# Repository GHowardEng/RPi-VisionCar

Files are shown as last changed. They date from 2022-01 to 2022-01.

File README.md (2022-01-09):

# RPi-VisionCar
## OpenCV vision-based maze car project

piCar



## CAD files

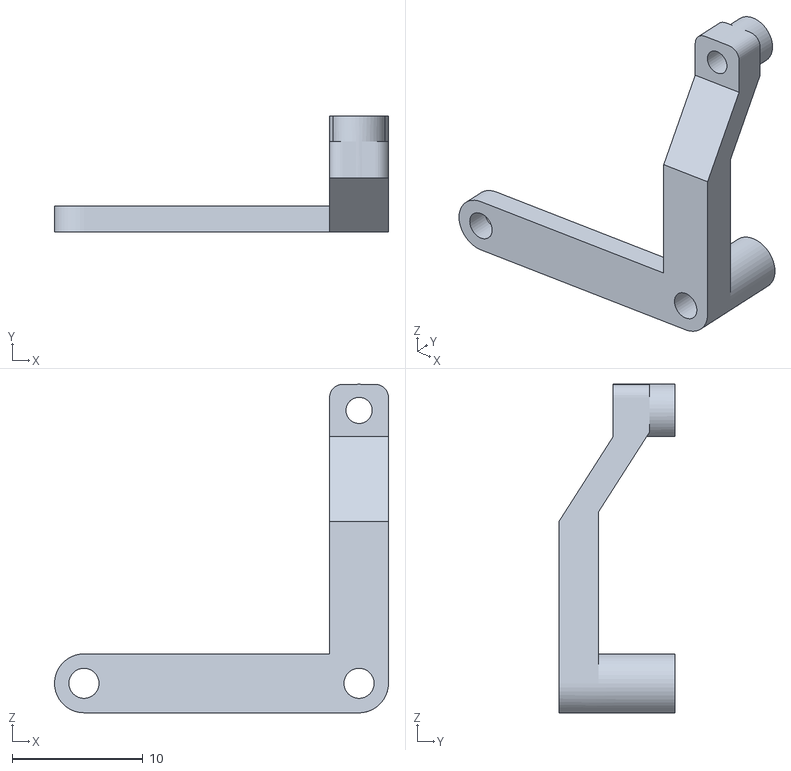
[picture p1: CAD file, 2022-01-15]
CAD/Components/CameraSpacer.stl
25.5 x 8.85 x 25.1

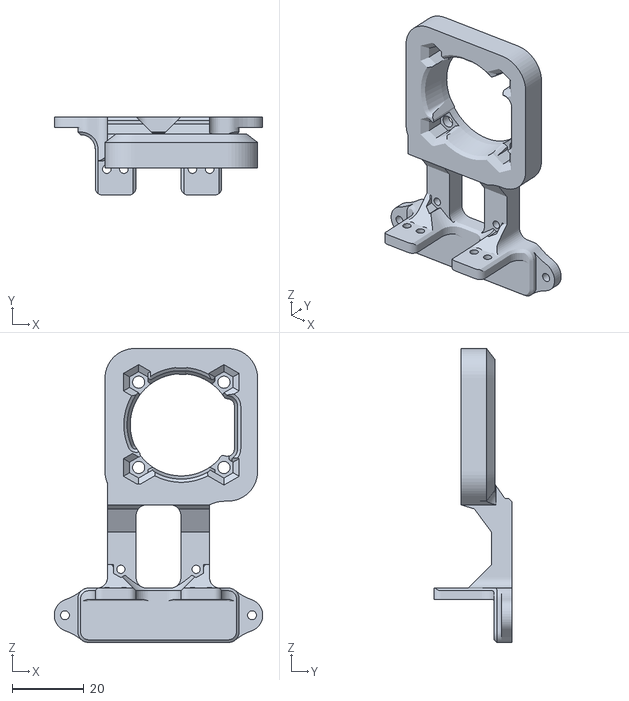
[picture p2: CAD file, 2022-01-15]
CAD/Components/SensorFanMount.stl
58.2 x 21.8 x 82.0

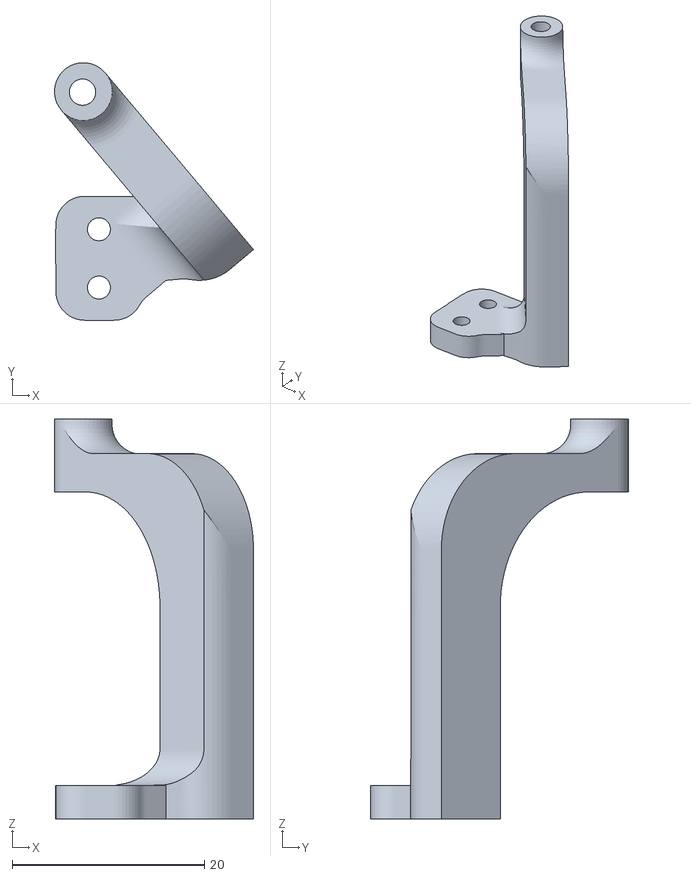
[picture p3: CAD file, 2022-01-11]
CAD/Components/PiMountFR.stl
20.7 x 26.8 x 41.6

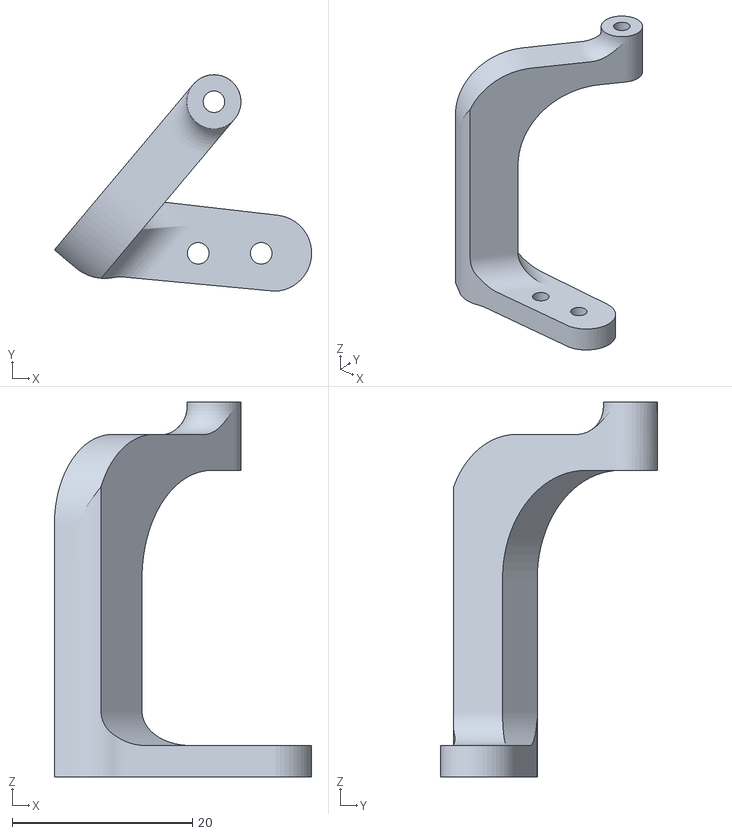
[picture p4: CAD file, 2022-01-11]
CAD/Components/PiMountLR.stl
28.6 x 24.1 x 41.6

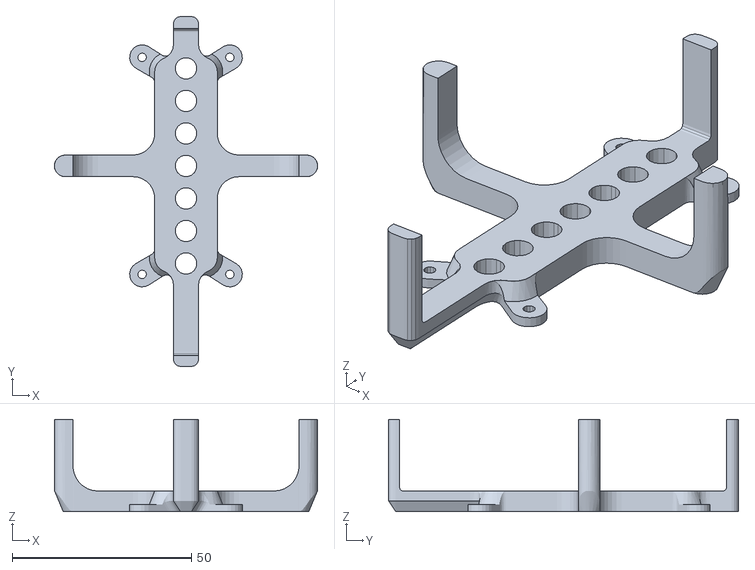
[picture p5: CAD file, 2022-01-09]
CAD/Components/BatteryBase.stl
73.5 x 97.8 x 25.7

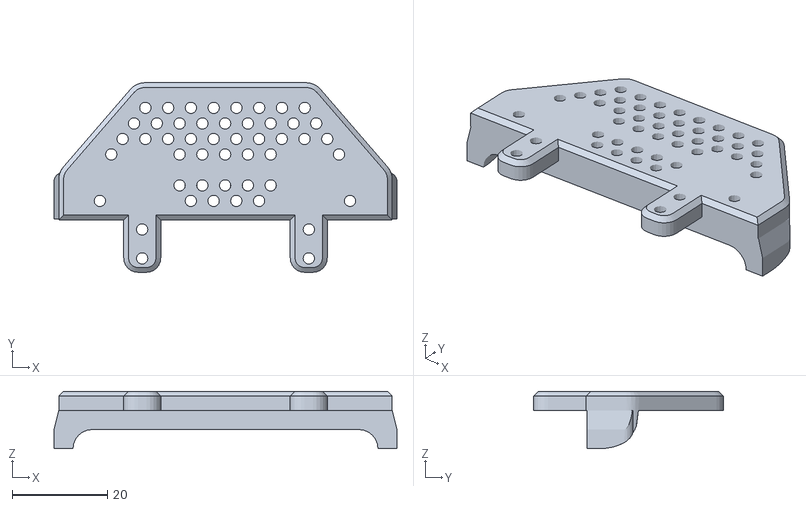
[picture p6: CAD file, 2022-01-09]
CAD/Components/CarFront.stl
72.0 x 39.8 x 12.0

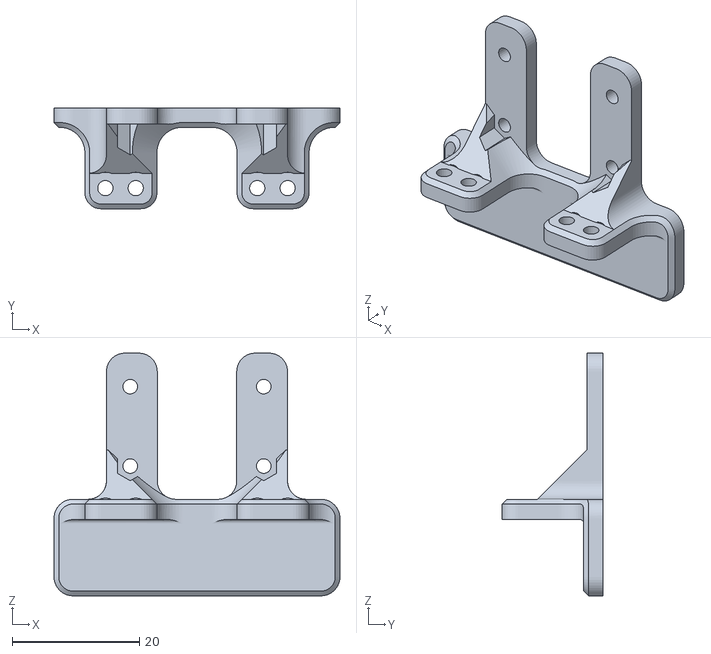
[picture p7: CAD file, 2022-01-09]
CAD/Components/Sensor Mount.stl
45.0 x 15.8 x 38.2

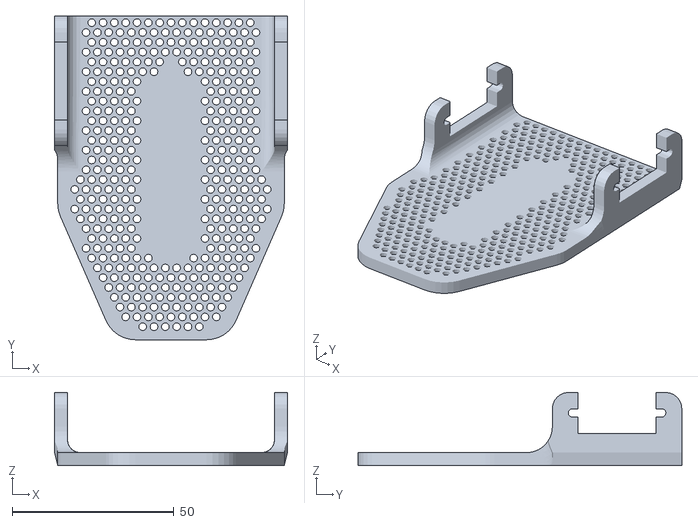
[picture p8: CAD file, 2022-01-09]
CAD/Components/CarBase v4.stl
72.0 x 100.0 x 22.6

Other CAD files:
CAD/Components/PiMountRR.stl

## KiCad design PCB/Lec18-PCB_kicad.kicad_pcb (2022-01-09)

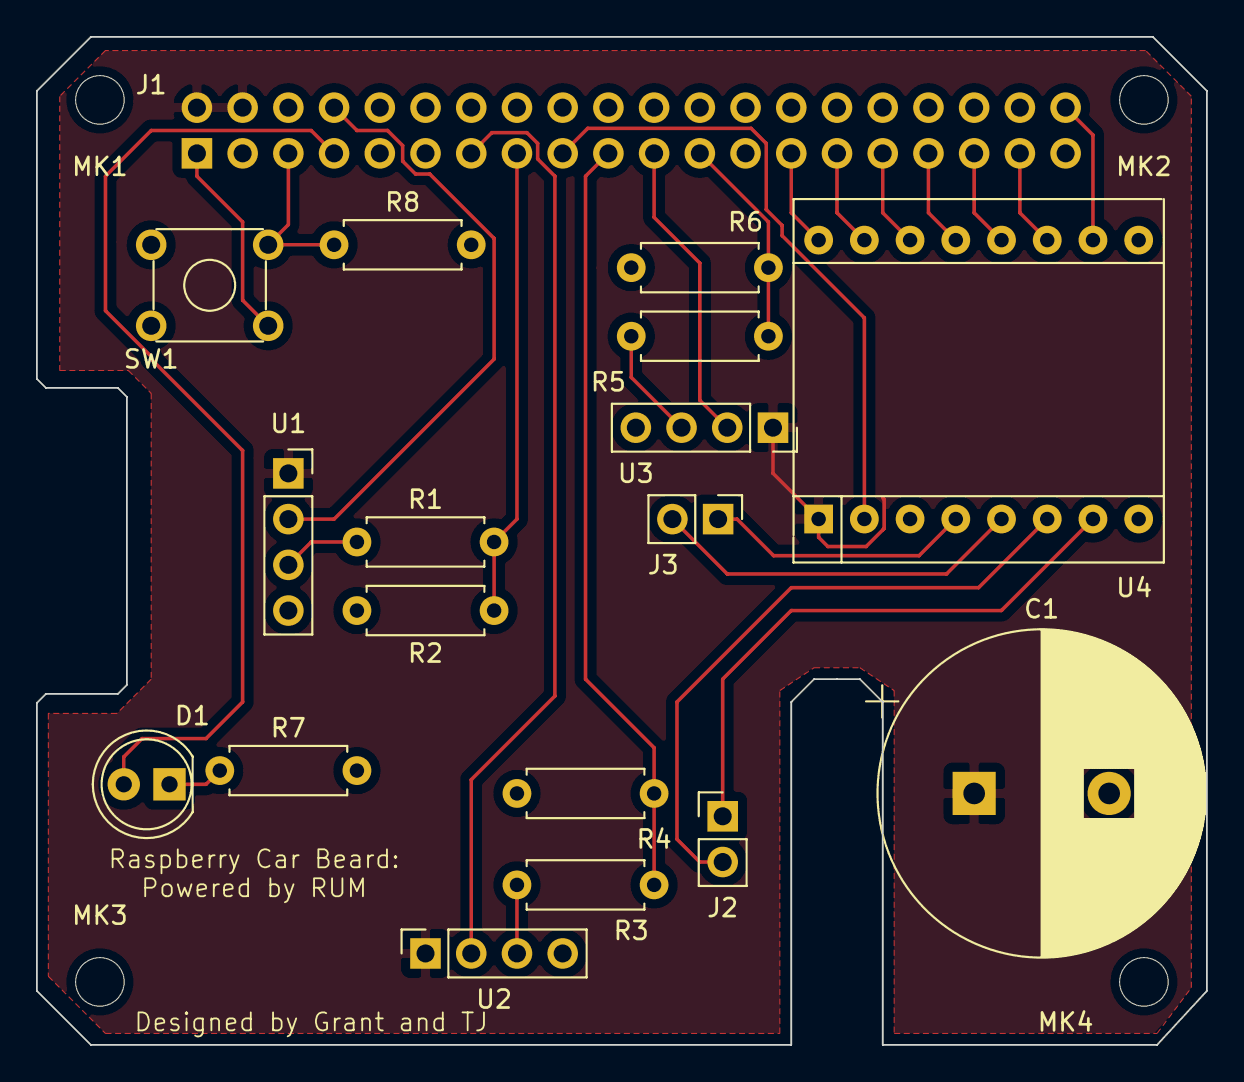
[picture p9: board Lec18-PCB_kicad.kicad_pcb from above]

Board: 2 copper layers, 65.0 x 56.0 mm, 22 parts (1 on the bottom side), 26 nets.

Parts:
C1: CAP; CP_Radial_D18.0mm_P7.50mm
D1: LED; LED_D5.0mm
J1: Raspberry_Pi_2_3; PinSocket_2x20_P2.54mm_Vertical
J2, J3: Conn_01x02_Male; PinHeader_1x02_P2.54mm_Vertical
MK1, MK2, MK3, MK4: M2.5; MountingHole_2.7mm_M2.5
R1, R2, R3, R4, R5, R6, R7, R8: R; R_Axial_DIN0207_L6.3mm_D2.5mm_P7.62mm_Horizontal
SW1: SW_Push_Dual; SW_TH_Tactile_Omron_B3F-10xx
U1, U2, U3: HC-SR04; PinSocket_1x04_P2.54mm_Vertical
U4: TB6612FNG_BREAKOUT; SparkFun_TB6612_foot

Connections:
+3V3: J1.1, J1.17, SW1.4, U4.2
+5V: C1.1, J1.2, J1.4, U1.1, U2.1, U3.1, U4.1
A01: J3.1, U4.4
A02: J3.2, U4.5
AIN1: J1.31, U4.14
AIN2: J1.29, U4.15
B01: J2.1, U4.7
B02: J2.2, U4.6
BIN1: J1.35, U4.12
BIN2: J1.37, U4.11
GND: C1.2, J1.6, J1.9, J1.14, J1.20, J1.25, J1.30, J1.34, J1.39, R2.2, R4.2, R6.2, R7.2, R8.2, U1.4, U2.4, U3.4, U4.3, U4.8, U4.9
LED: D1.2, J1.7
unnamed: D1.1, R7.1
P1_ECHO: J1.15, R1.2, R2.1
P2_ECHO: J1.19, R3.2, R4.1
P3_ECHO: J1.23, R5.2, R6.1
PUSH_BUTTON: J1.5, R8.1, SW1.2
PWMA: J1.27, U4.16
PWMB: J1.40, U4.10
STBY: J1.33, U4.13
U1_ECHO: R1.1, U1.3
U1_TRIG: J1.8, U1.2
U2_ECHO: R3.1, U2.3
U2_TRIG: J1.13, U2.2
U3_ECHO: R5.1, U3.3
U3_TRIG: J1.21, U3.2

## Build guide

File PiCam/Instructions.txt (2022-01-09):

To get the Raspberry Pi Cam V2.1 working with OpenCV

From: https://www.uco.es/investiga/grupos/ava/node/40

0) Make sure you have CMAKE installed

sudo apt-get update
sudo apt-get install cmake

1) Make sure camera is plugged into correct port
2) Turn on camera with sudo raspi-config
3) Copy raspicam-0.1.6 folder to Pi
4) Make raspicam project in a build folder

cd raspicam-0.1.6
mkdir build
cd build
cmake ..

5) Complete the install 

make
sudo make install
sudo ldconfig

6) Test by running the test build

Copy to your code folder the header file:
raspicam_cv.h

Add to your compile flags:
-I/usr/local/include/

Add to your link flags:
-lraspicam -lraspicam_cv 

* Note the >> operator was not implemented by the raspicam system, instead use:

cap.grab();
cap.retrieve(frame);

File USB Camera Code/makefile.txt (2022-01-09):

CC=g++

CFLAGS=-Wall `pkg-config --cflags opencv` -std=c++11 -c

LDFLAGS=-Wall `pkg-config --libs opencv` -o

all: cam

Sorting: main.o 
	$(CC) $(LDFLAGS) cam main.o -lwiringPi -lpigpio 
	
main.o: main.cpp
	$(CC) $(CFLAGS) main.cpp
	
clean:
	rm *o TestControl

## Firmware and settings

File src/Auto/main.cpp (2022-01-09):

#include <opencv2/opencv.hpp>
#include <opencv2/highgui/highgui.hpp>
#include "CControlPi.hpp"
#include "pigpio.h"
#include "wiringPi.h"
#include "CVision.hpp"
#include "libSonar.h"
#include <thread>
#include <iostream>
#include "raspicam_cv.h"


#define trigger1 15
#define echo1 3

#define trigger_left	2
#define echo_left		12

#define trigger_right	13
#define echo_right		14

using namespace std;
using namespace cv;


void imagefunc();

CControlPi ctrl;

void sonarPing();
void input_ch();


float distFront = 0;
float distRight = 0;
float distLeft = 0;

int result = 0;
int run = 0;
int turn = 0;
int right_count = 0;
string ch;

bool thread_pause;
bool thread_exit;

enum mode_state { MANUAL = 0, AUTO };

cv::Mat image;
cv::Mat crop;

int main()
{
	CVision vision;
	Mat frame;
	string tx;
	int input = 0;

	thread_exit = false;
	
	std::thread t1(&input_ch);
	t1.detach();
	
	std::thread t2(&imagefunc);
	t2.detach();	// Start image thread and detach
	
	waitKey(10);
	delay(2000);
	
	std::thread t3(&sonarPing);
	t3.detach();	// Start sonar measurement thread and detach
		
    while (ch != "q")
	{
		//vision.frame = crop;		// Input new camera image
		vision.frame = crop.clone();
		ctrl.get_data(DIGITAL, SW, input);
		
		thread_pause = true; 	// Pause image transmission thread
	
		result = vision.nav_vid(); // Process image and detect colour
		//cout << "Front: " << distFront << " cm. Left: " << distLeft << " cm. Right: " << distRight << "\n";

		imshow("result", vision.frame);
		waitKey(1);
	
		
		if (ch == "r")
		{
			run = 1;
			ctrl.set_data(DIGITAL, LED, 1);
		}
		
		if (ch == "x" || (run == 1 && input))
		{
			ch = "0";
			run = 0;
			right_count = 0;
			ctrl.stop();
			ctrl.drive = STOP;
			ctrl.set_data(DIGITAL, LED, 0);
		}
		


		
		//cout << "NAV\n";
		if (distFront > 15 && ctrl.drive == FORWARD)
		{
			if (result != 0)
			{
				if((vision.bound.x - (vision.frame.size().width - (vision.bound.x + vision.bound.width))) > 25)
				{
					cout << "\nRIGHT";
					ctrl.correct(RIGHT);
				}
					
				else if (((vision.frame.size().width - (vision.bound.x + vision.bound.width)) - vision.bound.x) > 25)
				{
					cout << "\nLEFT";
					ctrl.correct(LEFT);
				}
			}
		}
		

		if (result == GREEN)	// Turn based on navigation colour in picture
		{
			//cout << "\nGreen\n";
			//imshow("result", vision.frame);
			//waitKey(2);
			
			if(run && distFront < 13 && ctrl.drive == STOP)
			{
				turn = 1;
				ctrl.turn(RIGHT);
				right_count += 1;
				cout << right_count << "\n";
				while(distFront < 15){}
				turn = 0;
			}
			
			//cout << "\n" << vision.bound.x << "\n";
			//cout << vision.frame.size().width - (vision.bound.x + vision.bound.width) << "\n";
			
		}
		
		else if (result == RED)
		{
			
			//cout << "\nRed\n";
			//imshow("result", vision.frame);
			//waitKey(1);
			
			if(run && distFront < 13 && ctrl.drive == STOP)
			{
				turn = 1;
				ctrl.turn(LEFT);
				//cout << "\nRed\n";
				while(distFront < 15){}
				turn = 0;
			}
			
		}
					
		
	}

	ctrl.stop();
	cout << "Exit\n";
	
	delay(100);
	thread_exit = true;
	delay(500);
	ctrl.set_data(DIGITAL, LED, 0);
	return 0;
}



void imagefunc()
{
	raspicam::RaspiCam_Cv Camera;
    Camera.open();
	delay(1000);		// Open camera and give time for setup
	
	Camera.grab();
	Camera.retrieve ( image );	// Take new image from camera
	
	// Create rectangle object for cropping
	Rect box;
	box.x = 0;
	box.y = 400;	// Set box starting points
	box.width = image.size().width;
	box.height = image.size().height - box.y;	// Set box dimensions
	
	do
	{	
		Camera.grab();
		Camera.retrieve ( image );	// Take new image from camera
		flip(image, image, 0);		// Mirror vertically
		flip(image, image, 1);
		resize(image(box), crop, Size(), 0.45, 0.45);

		//imshow("Camera", image);
		//waitKey(10);
	} while (thread_exit != true);
	
	Camera.release();
	return;
}

void sonarPing()
{
	Sonar sonar1, sonar_left, sonar_right;
	
	sonar1.init(trigger1, echo1);
	sonar_left.init(trigger_left, echo_left);
	sonar_right.init(trigger_right, echo_right);
	
    float sample[4], sample_R[2], sample_L[2];
    
    do 
    {
		
		//delay(5);
		sample[3] = sample[2];
		sample[2] = sample[1];
		sample[1] = sample[0];
		sample[0] = sonar1.distance(20000);		// Shift samples
		
		if (sample[0] < sample[1] && sample[0] > sample[2])
		{
			distFront = sample[0];
		}
		else if(sample[0] > sample[1] && sample[0] < sample[2])
		{
			distFront = sample[0];
		}
		else if(sample[1] > sample[0] && sample[1] < sample[2])
		{
			distFront = sample[1];
		}
		else if(sample[1] > sample[2] && sample[1] < sample[0])
		{
			distFront = sample[1];
		}
		else if(sample[2] > sample[0] && sample[2] < sample[1])
		{
			distFront = sample[2];
		}
		else if(sample[2] > sample[1] && sample[2] < sample[0])
		{
			distFront = sample[2];
		}
		//cout << distFront << "\n";
			
		
		/*sample_R[1] = sample_R[0];
		sample_R[0] = sonar_right.distance(20000);		// Shift samples

		sample_L[1] = sample_L[0];
		sample_L[0] = sonar_left.distance(20000);		// Shift samples*/
		
		
		//distFront = (sample[0] + sample[1] + sample[2] + sample[3]) / 4; // Apply moving to average samples
		//distLeft = (sample_L[0] + sample_L[1]) / 2; // Apply moving to average samples
		//distRight = (sample_R[0] + sample_R[1]) / 2; // Apply moving to average samples 
		
		//distFront = sonar1.distance(25000);
		//distRight = sonar_right.distance(25000);
		//distLeft = sonar_left.distance(25000);
	
		if(distFront > 600)		// Sensor reads large distance when actually at zero
			distFront = 0;
		if(distRight > 600)		// Sensor reads large distance when actually at zero
			distRight = 0;
		if(distLeft > 600)		// Sensor reads large distance when actually at zero
			distLeft = 0;	
		
	if (distFront > 16 && run && !(turn))
	{
		//cout << "FWD\n";
		//ctrl.stop();
		ctrl.forward();
		ctrl.drive = FORWARD;	
	}
	else if(distFront < 11.5 && ctrl.drive == FORWARD && !(turn) && right_count < 6)
	{
		ctrl.stop();
		ctrl.drive = STOP;
		//delay(10);
	}
	if(ctrl.drive == FORWARD && distFront < 25 && right_count < 6)
	{
		ctrl.setSpeed(65);
	}
	else if (ctrl.drive == FORWARD && (distFront > 30 || right_count >= 6))
	{
		ctrl.setSpeed(85);
	}
	
	if (right_count >= 6 && distFront < 5)
	{
		ctrl.stop();
		ctrl.drive = STOP;
	}
		

	
					
	if ((ctrl.drive == FORWARD) && distLeft <= 2.5)
	{

	//ctrl.correct(RIGHT);
	//cout << "RIGHT, distLeft: " << distLeft << "\n";
	//delay(150);

	}
	else if ((ctrl.drive == FORWARD) && distRight <= 2.5)
	{
	
		//ctrl.correct(LEFT);
		//cout << "LEFT, distRight: " << distRight << "\n";
		//delay(150);
	
	}
	
		
	
	} while(thread_exit != true);
	
	return;
}

void input_ch()
{
	cout << "Auto mode running.";
	ch = "0";
	do
	{
		cin >> ch;
	}while(thread_exit != true);
	return;	
}

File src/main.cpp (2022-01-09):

#include <opencv2/opencv.hpp>
#include "CControlPi.hpp"
#include "pigpio.h"
#include "wiringPi.h"
#include "server.h"
#include "CVision.hpp"
#include "libSonar.h"
#include <thread>
#include <iostream>
#include "raspicam_cv.h"

#define trigger1 15
#define echo1 3

#define trigger_left	2
#define echo_left		12

#define trigger_right	13
#define echo_right		14

using namespace std;
using namespace cv;

Server serv;
void serverfunc();
void serverimagefunc();

CControlPi ctrl;

void sonarPing();
void status();

float distFront;
float distRight;
float distLeft;

int result = 0;

int run = 0;

bool thread_pause;
mutex mtx;

enum mode_state { MANUAL = 0, AUTO };
int mode = MANUAL;

cv::Mat image;
cv::Mat crop;

int main()
{
	CVision vision;
	Mat frame;
	string tx;
	int input = 0;
	
	
	serv._exit = false;
	std::thread t1(&serverfunc);
	t1.detach();	// Start server thread and detach
	
	// Wait until server starts up
	delay(3000);

	std::thread t2(&serverimagefunc);
	t2.detach();	// Start image thread and detach
	
	delay(2000);
	
	std::thread t3(&sonarPing);
	t3.detach();	// Start sonar measurement thread and detach
	
	std::thread t4(&status);
	t4.detach();
	
	cout << "\nServer Running. Send 'q' from Client to exit.\n";
	
    while (serv.str[0] != 'q')
	{
		crop.copyTo(vision.frame); 		// Input new camera image
		//vision.frame = image;
		ctrl.get_data(DIGITAL, SW, input);
		
	
		if (serv.str[0] == 'm')		// Switch modes when 'm' received
		{
			if (mode == MANUAL)
			{
				mode = AUTO;
				
				serv.reply = "AUTO MODE";
				cout << "\n" << serv.reply << "\n";
				send(serv.clientsock, serv.reply.c_str(), serv.reply.length(), 0);
			}
			else
			{
				mode = MANUAL;
				
				serv.reply = "MANUAL MODE";
				cout << "\n" << serv.reply << "\n";
				send(serv.clientsock, serv.reply.c_str(), serv.reply.length(), 0);
				ctrl.drive = STOP;
			}
			delay(1000);
		}
		
		if (mode == MANUAL)				// If in manual mode
		{
						
			thread_pause = false;		// Run image transmission thread
			delay(1);
			
			if(distFront < 10.5 && ctrl.drive == FORWARD)
			{
				ctrl.stop();
				ctrl.drive = STOP;
			}
			
			if (input)
				ctrl.stop();
			else
				ctrl.readInput(serv.str);	// Read manual inputs and control car
		}
		
		else 						// Else run in automatic mode
		{
			thread_pause = true; 	// Pause image transmission thread
		
			
			delay(100);
			cout << "Front: " << distFront << " cm. Left: " << distLeft << " cm. Right: " << distRight << "\n";
			
			
			if (serv.str[0] == 'r' || (run == 0 && input))
			{
				run = 1;
				ctrl.set_data(DIGITAL, LED, 1);
				
			}
			
			if (serv.str[0] == 'x' || (run == 1 && input))
			{
				run = 0;
				ctrl.stop();
				ctrl.drive = STOP;
				ctrl.set_data(DIGITAL, LED, 0);
				
			}
			
			if (run == 1)
			{
				if (distFront < 20)
					result = vision.nav_vid(); // Process image and detect colour
					serv.set_txim(vision.im);	// Transmit processed image	
					//imshow("vision", vision.im);
					//waitKey(1);
				if (ctrl.drive == STOP)
				{

					

				}
				
					
			}
		}

	}

	ctrl.stop();
	
	//serv._exit = true;
	delay(500);
	return 0;
}


// Start TCP server
void serverfunc()
{
	serv.start(4618);
}

// Send image to TCP server
void serverimagefunc()
{
	raspicam::RaspiCam_Cv Camera;
    Camera.open();
	delay(1000);		// Open camera and give time for setup
	
	Camera.grab();
	Camera.retrieve ( image );	// Take new image from camera
	
	// Create rectangle object for cropping
	Rect box;
	box.x = 100;
	box.y = 200;	// Set box starting points
	box.width = image.size().width - 2*box.x;
	box.height = image.size().height - 1.15*box.y;	// Set box dimensions
	
	do
	{	
		Camera.grab();
		Camera.retrieve ( image );	// Take new image from camera
		crop = image(box);
		flip(crop, crop, 0);		// Mirror vertically
		flip(crop, crop, 1);
		
		
		if(thread_pause == false)	// If not paused, set image for transmission
		{
			serv.set_txim(crop);
		}
		
	} while (serv._exit != true);
}

void sonarPing()
{
	Sonar sonar1, sonar_left, sonar_right;
	
	sonar1.init(trigger1, echo1);
	sonar_left.init(trigger_left, echo_left);
	sonar_right.init(trigger_right, echo_right);
	
    float sample[2], sample_R[2], sample_L[2];
    
    do 
    {
		//delay(5);
		
		/*sample[1] = sample[0];
		sample[0] = sonar1.distance(25000);		// Shift samples
		
		sample_R[1] = sample_R[0];
		sample_R[0] = sonar_right.distance(25000);		// Shift samples

		sample_L[1] = sample_L[0];
		sample_L[0] = sonar_left.distance(25000);		// Shift samples*/
		
		mtx.lock();
		/*distFront = (sample[0] + sample[1]) / 2; // Apply moving to average samples
		distLeft = (sample_L[0] + sample_L[1]) / 2; // Apply moving to average samples
		distRight = (sample_R[0] + sample_R[1]) / 2; // Apply moving to average samples
		*/
		distFront = sonar1.distance(25000);
		distRight = sonar_right.distance(25000);
		distLeft = sonar_left.distance(25000);
	
		if(distFront > 600)		// Sensor reads large distance when actually at zero
			distFront = 0;
		if(distRight > 600)		// Sensor reads large distance when actually at zero
			distRight = 0;
		if(distLeft > 600)		// Sensor reads large distance when actually at zero
			distLeft = 0;	
		mtx.unlock();
		
		if ((ctrl.drive == FORWARD) && distLeft <= 2.2)
		{
			mtx.lock();
			ctrl.correct(RIGHT);
			cout << "RIGHT, distLeft: " << distLeft << "\n";
			delay(100);
			mtx.unlock();
		}
		else if ((ctrl.drive == FORWARD) && distRight <= 2.2)
		{
			mtx.lock();
			ctrl.correct(LEFT);
			cout << "LEFT, distRight: " << distRight << "\n";
			delay(100);
			mtx.unlock();
		}
		
		if(distFront < 11.5 && ctrl.drive == FORWARD)
		{
			mtx.lock();
			ctrl.stop();
			ctrl.drive = STOP;
			mtx.unlock();
	

			if (result == GREEN)	// Turn based on navigation colour in picture
			{
				ctrl.drive = STOP;
				cout << "\nGreen\n";
				ctrl.turn(RIGHT);
			}
			
			else if (result == RED)
			{
				ctrl.drive = STOP;
				cout << "\nRed\n";
				ctrl.turn(LEFT);
			}
		}
			
		else if (distFront > 25.0 && mode == AUTO && run )
		{
			mtx.lock();
			ctrl.forward();
			ctrl.drive = FORWARD;
			mtx.unlock();
			
		}
	
	} while(serv._exit != true);
}

void status()
{
	do
	{
		while(mode != MANUAL){}
		delay(10);
		gpioWrite(LED, gpioRead (STBY) );
	} while(serv._exit != true);
}

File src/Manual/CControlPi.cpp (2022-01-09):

#include "CControlPi.hpp"
#include "pigpio.h"
#include "wiringPi.h"
#include "softPwm.h"

#include <iostream>

#define max 65
using namespace std;

CControlPi::CControlPi()
{
	wiringPiSetup();
	softPwmCreate (PWMa, 100, 100);
	softPwmCreate (PWMb, 100, 100);
	
	gpioInitialise();
	gpioSetMode(Ai1, PI_OUTPUT);
	gpioSetMode(LED, PI_OUTPUT);
	gpioSetMode(SW,	 PI_INPUT);
	gpioSetMode(Ai2, PI_OUTPUT);
	gpioSetMode(Bi1, PI_OUTPUT);
	gpioSetMode(Bi2, PI_OUTPUT);
	gpioSetMode(STBY, PI_OUTPUT);
	
	//CControlPi::stop();
}
bool CControlPi::get_data(int type, int channel, int &value)
{
	if (type == DIGITAL)
	{
		value = gpioRead (channel);
		return true;
	}
	
	else if (type == ANALOG)
	{
		unsigned char inBuf[3];
		char cmd[] = { 1, 128, 0 };
		
		int handle = spiOpen(channel, 200000, 3);
		
		spiXfer(handle, cmd, (char*) inBuf, 3);
		value = ((inBuf[1] & 3) << 8) | inBuf[2];
		
		spiClose(handle);
		
		return true;
	}
	return false;
}

bool CControlPi::set_data(int type, int channel, int value)
{
	if (type == DIGITAL)
	{
		gpioWrite(channel, value);
		return true;
	}
	
	else if (type == SERVO)
	{
		gpioServo(channel, value);
		return true;
	}
	
	return false;
}

int CControlPi::get_analog(int channel, int &value)
{
	if (get_data(ANALOG, channel, value))
	{
		return (100 * (value)) / 1023;
	}
	return false;

}

int CControlPi::get_button(int channel, int index)
{
	int value;
	get_data(DIGITAL, channel, value);

	if (value != lastval[index])
	{
		lastval[index] = value;
		delay(2);
		
		get_data(DIGITAL, channel, value);
		if (value == 0)
		{
			return 1;
		}
	}
	

	return 0;
}

void CControlPi::print_menu(void)
{

	cout << "\n\n******************************";
	cout << "\n\n(B)utton Count";
	cout << "\n(D)igital Input/Output";
	cout << "\n(A)nalog Inputs";
	cout << "\n(S)ervo Test";
	cout << "\n(C)ontrol Servo";
	cout << "\n(Q)uit";
	cout << "\n\nCommand> ";

}

void CControlPi::forward(void)
{	
	CControlPi::setSpeed(0);
	CControlPi::set_data(DIGITAL, STBY, 1);		// Take out of standby
	
	CControlPi::set_data(DIGITAL, Ai1, 0);		// Activate motor (CCW)
	CControlPi::set_data(DIGITAL, Ai2, 1);
	
	CControlPi::set_data(DIGITAL, Bi1, 1);		// Activate motor (CW)
	CControlPi::set_data(DIGITAL, Bi2, 0);		// Directions reversed due to motor placement
	
	if (CControlPi::drive != FORWARD){
		cout << "accel\n";
		for (int i = 5; i < max; i+=5){
			 softPwmWrite(PWMa, i );
			softPwmWrite(PWMb, i - 2);
			delay(10);
		}
	}
	softPwmWrite(PWMa, max );
	softPwmWrite(PWMb, max - 2);
	
}

void CControlPi::reverse(void)
{
	//CControlPi::stop();
	
	softPwmWrite(PWMa, max - 15 );
	softPwmWrite(PWMb, max - 21);
	
	CControlPi::set_data(DIGITAL, STBY, 1);		// Take out of standby
			
	CControlPi::set_data(DIGITAL, Ai1, 1);		// Activate motor (CW)
	CControlPi::set_data(DIGITAL, Ai2, 0);
	
	CControlPi::set_data(DIGITAL, Bi1, 0);		// Activate motor (CCW)
	CControlPi::set_data(DIGITAL, Bi2, 1);		// Directions reversed due to motor placement
}

void CControlPi::stop(void)
{	
	if(CControlPi::drive != STOP)
	{
		for(int i = 40; i > 0; i-=5){
			CControlPi::setSpeed(i);
			delay(10);
		}
	}
	
		CControlPi::set_data(DIGITAL, Bi1, 0);		// De-activate motor
		CControlPi::set_data(DIGITAL, Bi2, 0);
		delay(100);
		
		CControlPi::set_data(DIGITAL, Ai1, 0);		// De-activate motor
		CControlPi::set_data(DIGITAL, Ai2, 0);
		
		CControlPi::set_data(DIGITAL, STBY, 0);		// Put in standby
		
		
		

}

void CControlPi::turn(int dir)
{
	
	CControlPi::set_data(DIGITAL, STBY, 1);		// Take out of standby
		
	if (dir == RIGHT)
	{
		CControlPi::setSpeed(60);
		CControlPi::set_data(DIGITAL, Ai1, 0);		// Activate motor (CW)
		CControlPi::set_data(DIGITAL, Ai2, 0);
		
		CControlPi::set_data(DIGITAL, Bi1, 1);		// Activate motor (CW)
		CControlPi::set_data(DIGITAL, Bi2, 0);
		delay(530);
	}
	
	else if (dir == LEFT)
	{
		CControlPi::setSpeed(61);
		CControlPi::set_data(DIGITAL, Ai1, 0);		// Activate motor (CW)
		CControlPi::set_data(DIGITAL, Ai2, 1);
		
		CControlPi::set_data(DIGITAL, Bi1, 0);		// Activate motor (CW)
		CControlPi::set_data(DIGITAL, Bi2, 0);
		delay(540);
	}
	
	CControlPi::set_data(DIGITAL, Bi1, 0);		// De-activate motor
	CControlPi::set_data(DIGITAL, Bi2, 0);
	
	
	CControlPi::set_data(DIGITAL, Ai1, 0);		// De-activate motor
	CControlPi::set_data(DIGITAL, Ai2, 0);
	
	CControlPi::set_data(DIGITAL, STBY, 0);		// Put in standby
}

void CControlPi::correct(int dir)		// Reduce motor speed on one side for corrective turn
{
	if (dir == RIGHT)
	{
		softPwmWrite(PWMa, max - 35);
		softPwmWrite(PWMb, max + 5);
	}
	
	else if (dir == LEFT)
	{
		softPwmWrite(PWMb, max - 35);
		softPwmWrite(PWMa, max + 5);
	}
	
	delay(25);
	
	CControlPi::forward();
}

void CControlPi::small_turn(int dir)
{
	
	CControlPi::set_data(DIGITAL, STBY, 1);		// Take out of standby
		
	if (dir == RIGHT)
	{
		CControlPi::setSpeed(60);
		CControlPi::set_data(DIGITAL, Ai1, 0);		// Activate motor (CW)
		CControlPi::set_data(DIGITAL, Ai2, 0);
		
		CControlPi::set_data(DIGITAL, Bi1, 1);		// Activate motor (CW)
		CControlPi::set_data(DIGITAL, Bi2, 0);
		delay(40);
	}
	
	else if (dir == LEFT)
	{
		CControlPi::setSpeed(61);
		CControlPi::set_data(DIGITAL, Ai1, 0);		// Activate motor (CW)
		CControlPi::set_data(DIGITAL, Ai2, 1);
		
		CControlPi::set_data(DIGITAL, Bi1, 0);		// Activate motor (CW)
		CControlPi::set_data(DIGITAL, Bi2, 0);
		delay(40);
	}
	
	CControlPi::set_data(DIGITAL, Bi1, 0);		// De-activate motor
	CControlPi::set_data(DIGITAL, Bi2, 0);
	
	
	CControlPi::set_data(DIGITAL, Ai1, 0);		// De-activate motor
	CControlPi::set_data(DIGITAL, Ai2, 0);
	
	CControlPi::set_data(DIGITAL, STBY, 0);		// Put in standby
}

void CControlPi::setSpeed(int val)
{
	if ((val >= 0) && (val < 70))
	{
		softPwmWrite(PWMa, val);
		softPwmWrite(PWMb, val -3);
	}
	else 
	{
		softPwmWrite(PWMa, val);
		softPwmWrite(PWMb, val -5);
	}
		
}
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

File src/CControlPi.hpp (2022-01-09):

#pragma once
#include <string>

using namespace std;

enum TYPE { DIGITAL = 0, ANALOG, SERVO };
enum DIR { LEFT = 0, RIGHT};

#define Ai1 6
#define Ai2 5
#define PWMa 30		// Control pins for motor A

#define Bi1	19
#define Bi2 26
#define PWMb 29		// Control pins for motor B

#define STBY 13		// Motor controller standby pin

#define LED 4 		// BCM pin for PiHAT LED
#define SW	17		// BCM pin for PiHAT pushbutton

#define SERVO_MAX 2500
#define SERVO_MIN 700

#define pwmMax 90
#define pwmMid 60

enum drive_state { STOP = 0, FORWARD, REVERSE };

class CControlPi
{
private:
	int lastval[5];  ///< Stores previous button state for de-bouncing
	int speedA = 0, speedB = 0;
	
public:
	CControlPi();
	int drive = STOP;
	bool get_data(int type, int channel, int &value);
	bool set_data(int type, int channel, int value);
	int get_button(int channel, int index);
	int get_analog(int channel, int &value);
	void print_menu(void);
	
	void turn(int dir);
	void forward(void);
	void reverse(void);
	void stop(void);
	void correct(int dir);
	void setSpeed(int val);
	void readInput(string input);
	
};

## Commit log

2022-01-09 Additional project files
    [Lec18-PCB_kicad-B_Cu.gbl, Lec18-PCB_kicad-B_Mask.gbs, Lec18-PCB_kicad-Edge_Cuts.gm1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]
2022-01-09 Add working CAD files
    [BatteryBase.stl, CarBase v4.stl, CarBaseAcc v24.step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]
2022-01-11 New .stl files
    [PiMountFR.stl, PiMountLR.stl, PiMountRR.stl]
2022-01-14 Add Pose Estimation programs and other openCV python scripts
    - Calibration, Chessboard pose, ArUco pose
    [calibration.yaml]
2022-01-15 Update CAD assembly and components
    [BatteryBase.stl, CameraSpacer.stl, CarBase v4.stl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]
2022-01-15 Update CAD assembly
